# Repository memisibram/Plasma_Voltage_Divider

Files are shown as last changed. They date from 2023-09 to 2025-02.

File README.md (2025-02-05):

# Plasma_Voltage_Divider
Plasma Voltage Divider

### About the project
An electronic circuit for reading voltage from plasma machines.

Plasma machines output up to 200v. We need a voltage divider to read this voltage and use it in projects such as THC. This circuit gives output between 0 and 5v by dividing the voltage for use in controllers such as Atmega.

 - Video: [https://www.youtube.com/watch?v=IpVODe6NoKA](https://youtu.be/YBrCMQDwGMo)

### Drawing program
It was prepared using the Cross Platform and Open Source Electronics Design Automation Suite KiCad 6.0.

### Required components:
 - 2 x	5.1v - Zener Diode for D1,D2
 - 2 x	10µF/25V or 16v- Electrolytic Capacitor for C6,C7
 - 2 x	9x12 - 30mH Radial D9.5mm P5.00mm inductor for L1,L2
 - 4 x	1nF - Ceramic disc for C5,C2,C3,C4
 - 2 x	LM358 - op-amp for U1,U3
 - 1 x	100R - 1/4w or 1/2w for R5
 - 1 x	B1212S-1WR3 for BS1
 - 2 x	47k - 1/4w or 1/2w for R4,R6
 - 1 x	47nF 1KV  - High Voltage Ceramic Capacitor for C1
 - 1 x	HCNR200 - high-linearity analog optocoupler for U2
 - 1 x	3k9 - 5W - Power Resistor Ceramic Cement Resistor for R3
 - 2 x	100k - 5W - Power Resistor Ceramic Cement Resistor for R1,R2
 - 1 x	1x02_P5.00mm_Horizontal - Plasma Negative Electrode Terminal for J1
 - 1 x	1x02_P5.00mm_Horizontal - Plasma Positive Work Terminal for J3
 - 1 x	1x04_P5.00mm_Horizontal - Power / Output Terminal for J2

### Pictures

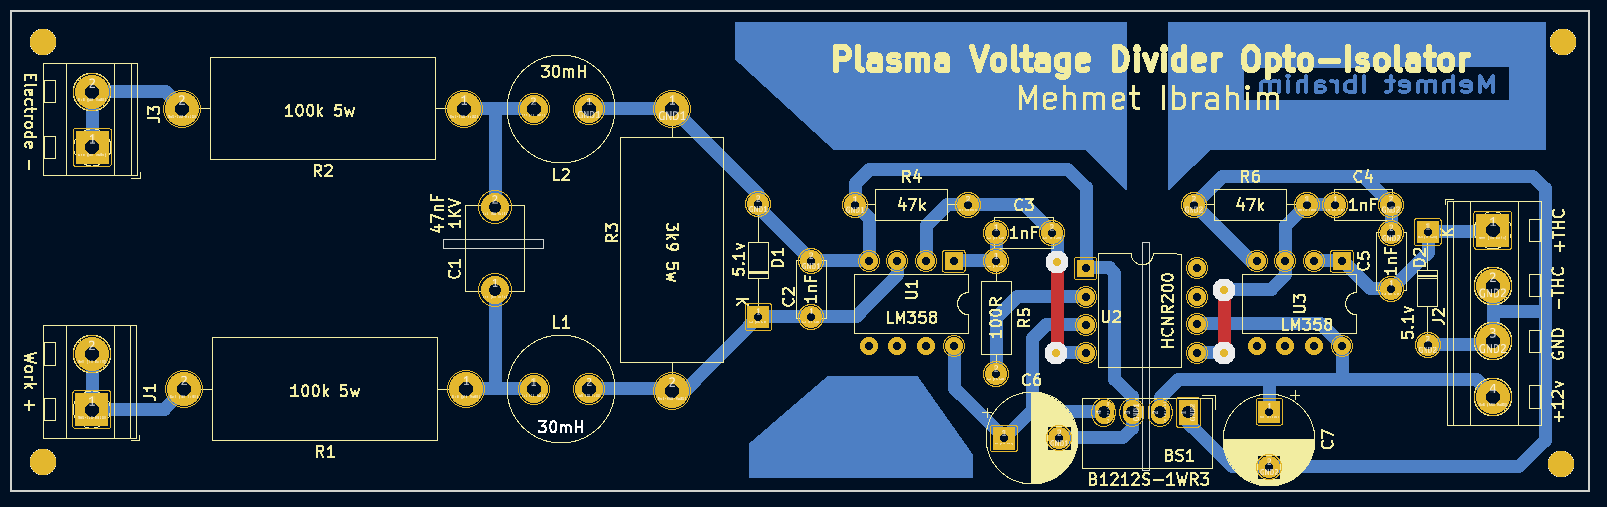
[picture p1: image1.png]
Plasma Voltage Divider Image1

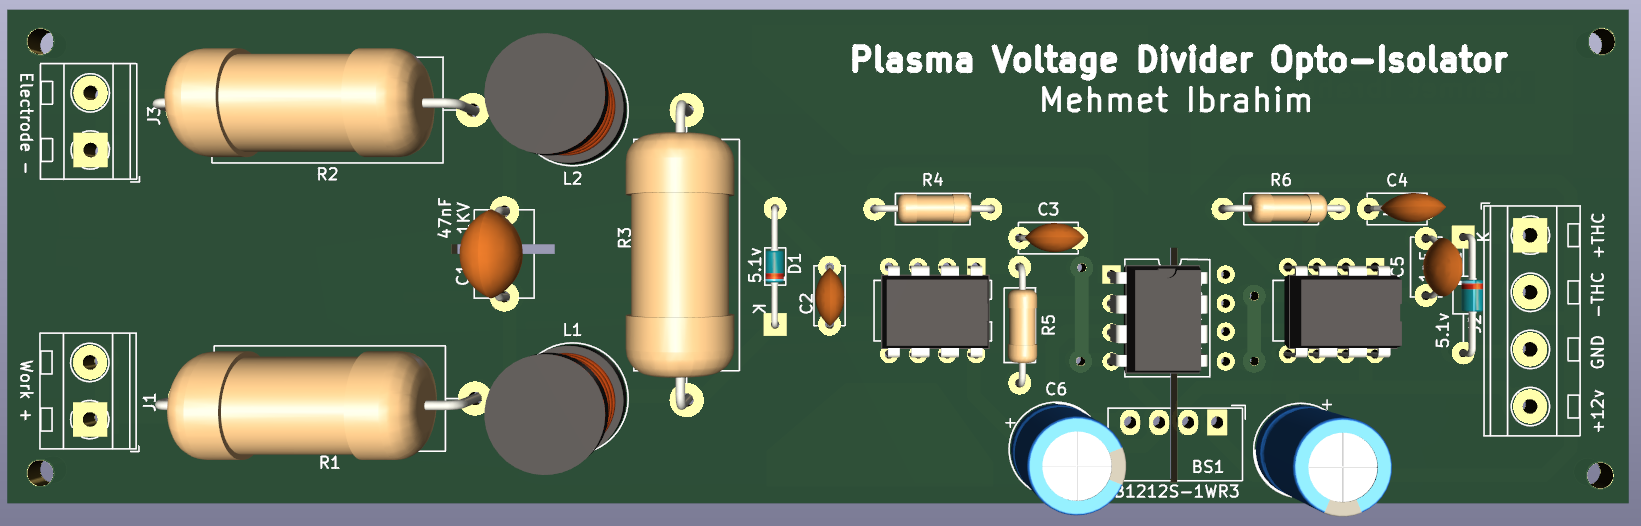
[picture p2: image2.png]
Plasma Voltage Divider Image2

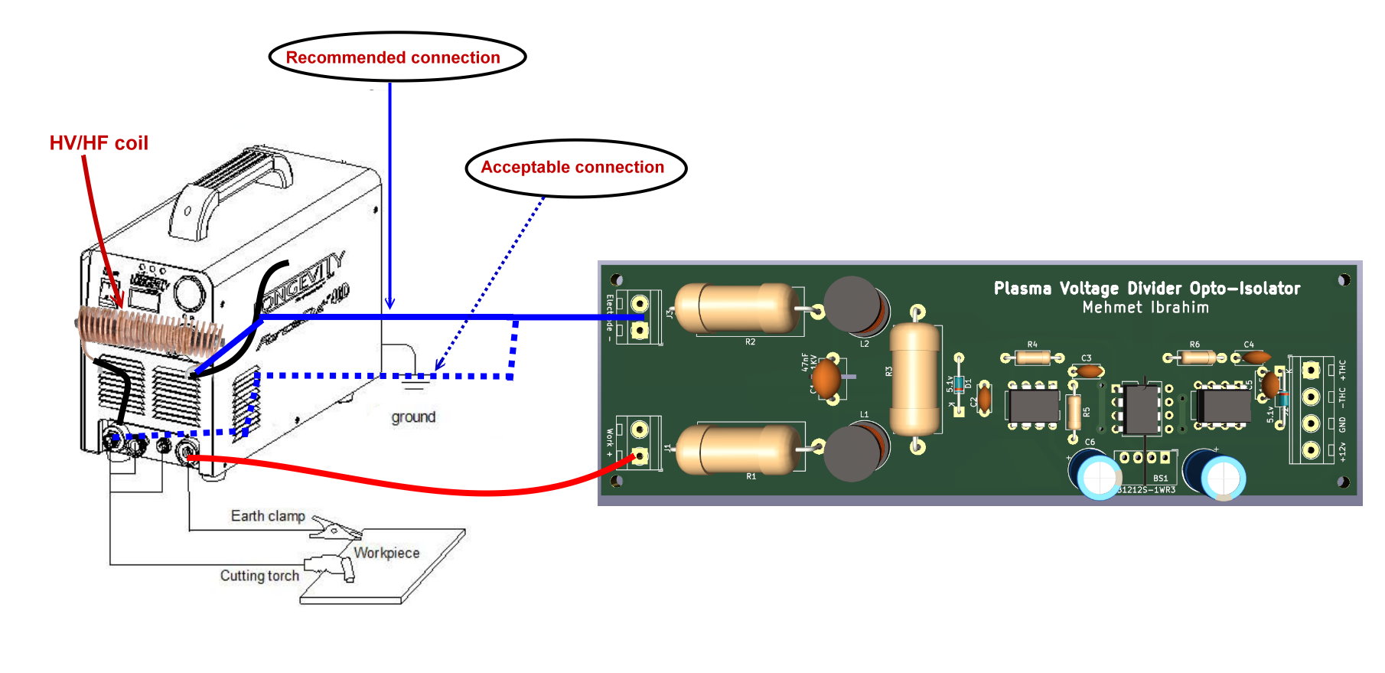
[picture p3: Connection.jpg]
Plasma Voltage Divider Image3


### License GNU GPL v3.0

### Donation

  -  Paypal: memisibram@gmail.com or https://www.paypal.me/memisibram

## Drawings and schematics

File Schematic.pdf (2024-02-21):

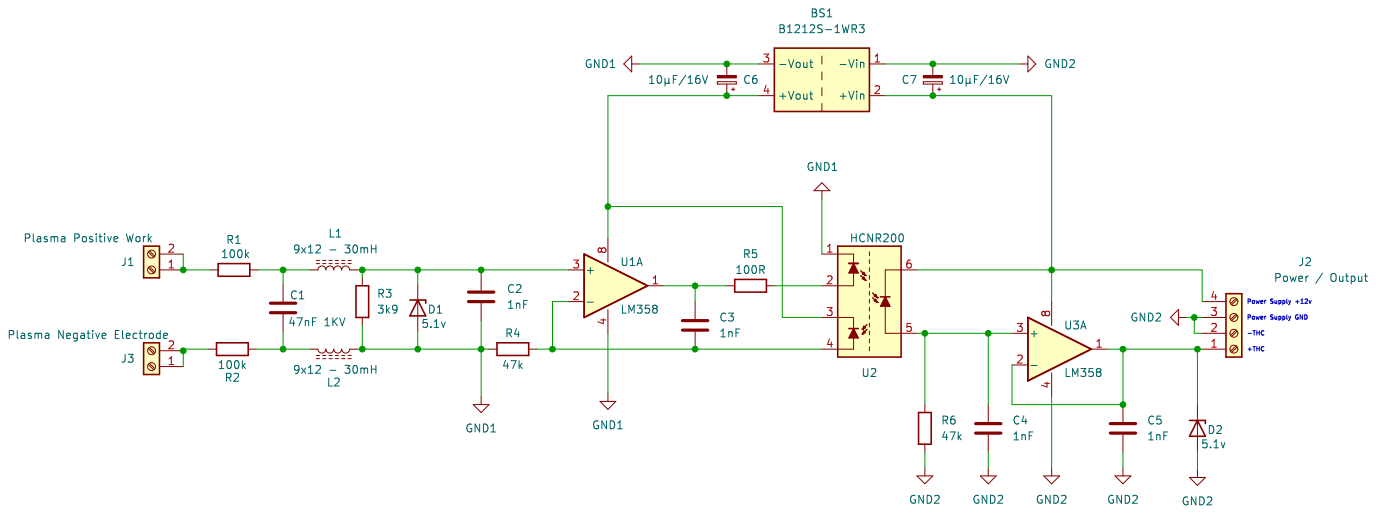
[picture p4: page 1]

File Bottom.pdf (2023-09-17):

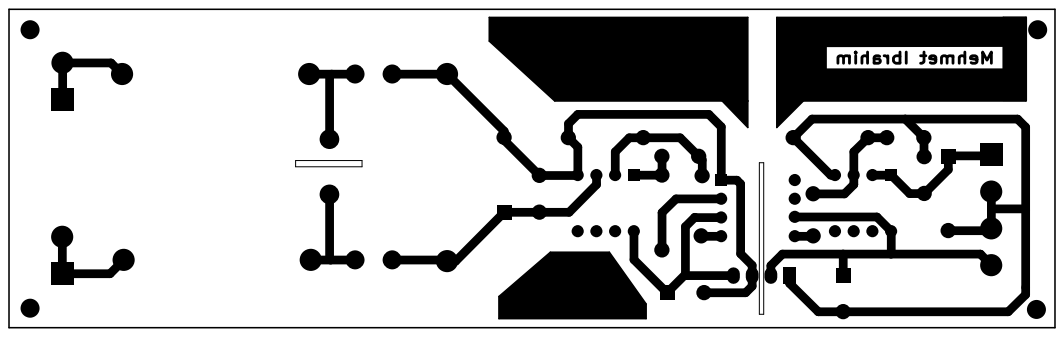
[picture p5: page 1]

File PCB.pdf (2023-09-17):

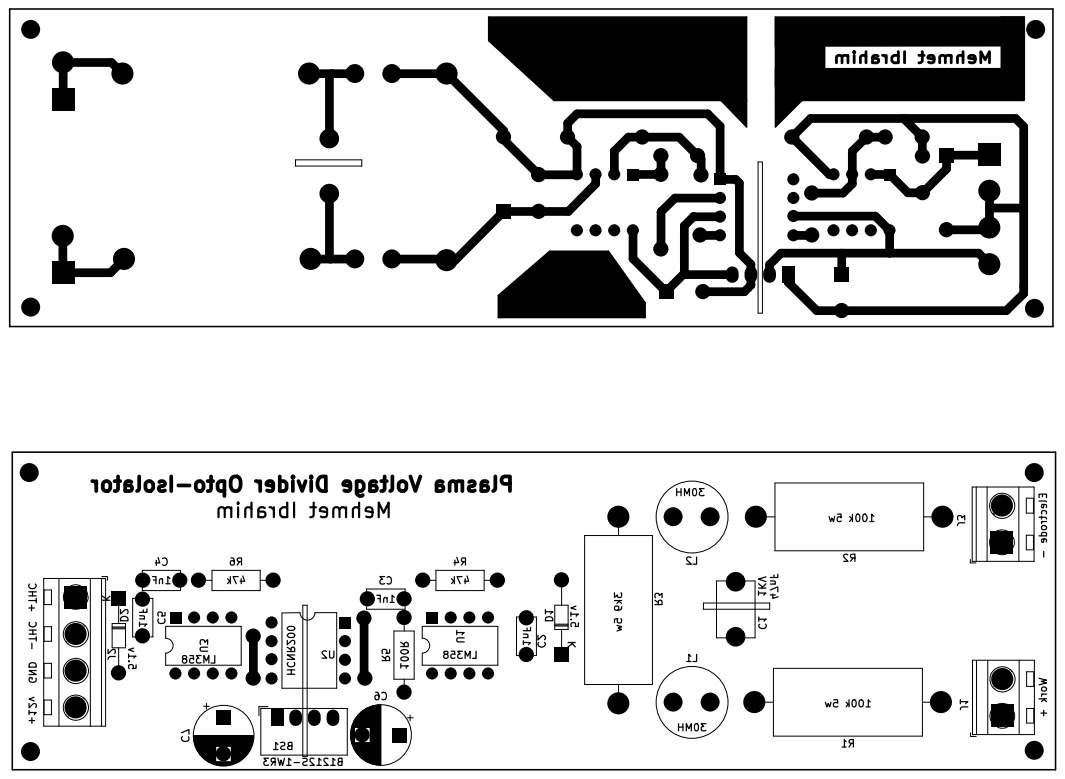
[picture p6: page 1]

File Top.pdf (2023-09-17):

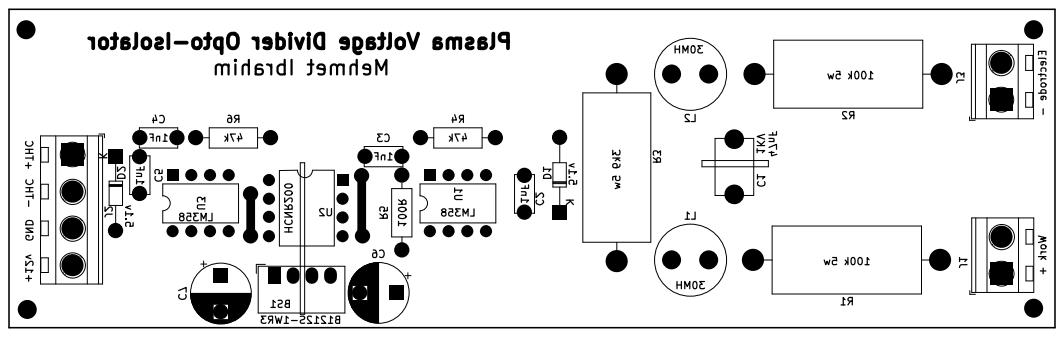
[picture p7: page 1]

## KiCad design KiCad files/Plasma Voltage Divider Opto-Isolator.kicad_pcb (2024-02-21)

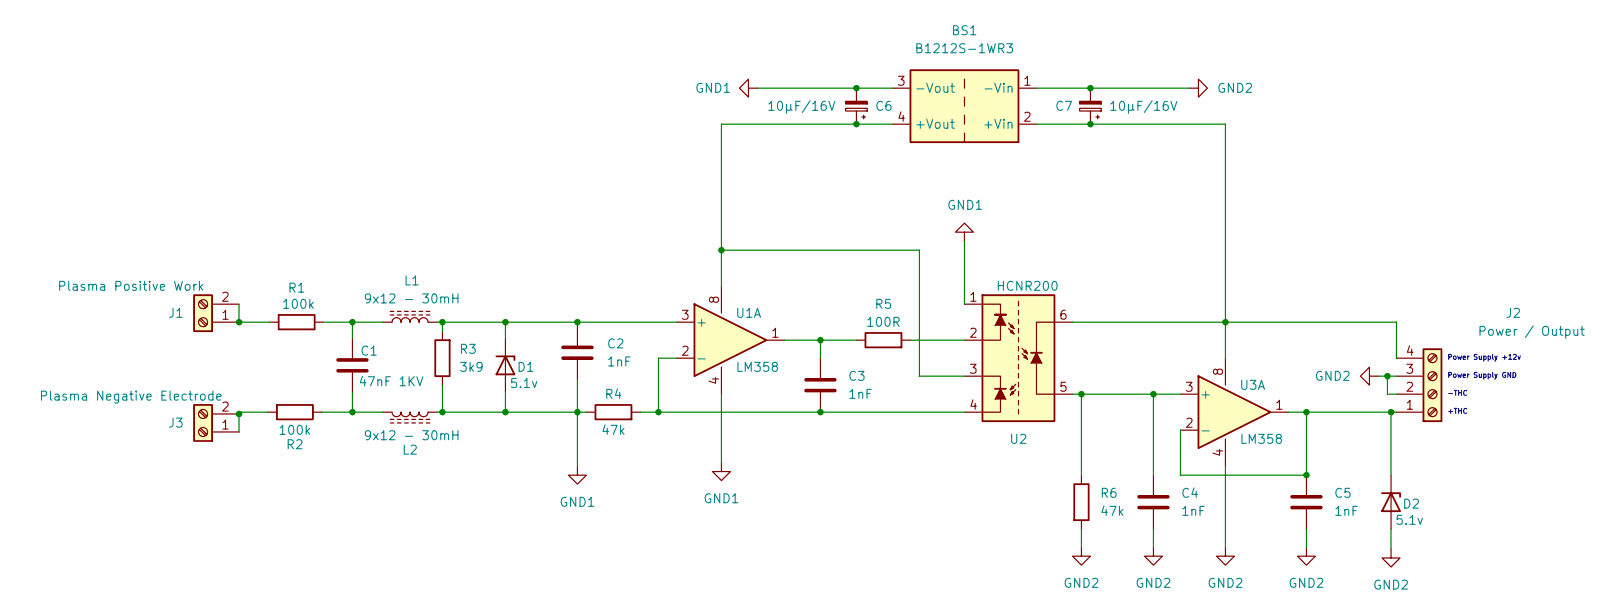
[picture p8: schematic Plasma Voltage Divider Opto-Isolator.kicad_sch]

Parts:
BS1: B1212S-1WR3; Converter_DCDC_Murata_MEE1SxxxxSC_THT
C1: 47nF 1KV; C_Disc_D7.5mm_W5.0mm_P7.50mm
C2, C3, C4, C5: 1nF; C_Disc_D5.0mm_W2.5mm_P5.00mm
C6, C7: 10µF/16V; CP_Radial_D8.0mm_P5.00mm
D1, D2: 5.1v; D_DO-34_SOD68_P10.16mm_Horizontal
J1: Plasma Positive Work; TerminalBlock_MetzConnect_Type094_RT03502HBLU_1x02_P5.00mm_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
J2: Power / Output; TerminalBlock_MetzConnect_Type094_RT03504HBLU_1x04_P5.00mm_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
J3: Plasma Negative Electrode; TerminalBlock_MetzConnect_Type094_RT03502HBLU_1x02_P5.00mm_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
L1, L2: 9x12 - 30mH; L_Radial_D9.5mm_P5.00mm_Fastron_07HVP
R1, R2: 100k; R_Axial_DIN0922_L20.0mm_D9.0mm_P25.40mm_Horizontal
R3: 3k9; R_Axial_DIN0922_L20.0mm_D9.0mm_P25.40mm_Horizontal
R4, R6: 47k; R_Axial_DIN0207_L6.3mm_D2.5mm_P10.16mm_Horizontal
R5: 100R; R_Axial_DIN0207_L6.3mm_D2.5mm_P10.16mm_Horizontal
U1, U3: LM358; DIP-8_W7.62mm
U2: HCNR200; DIP-8_W7.62mm

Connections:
GND1: BS1.3 (-Vout), C2.2, C6.2, D1.2 (A), L2.1, R3.1, R4.1, U1.4 (V-), U2.1
GND2: BS1.1 (-Vin), C4.2, C5.2, C7.2, D2.2 (A), J2.2, J2.3, R6.2, U3.4 (V-)
unnamed: BS1.2 (+Vin), C7.1, J2.4, U2.6, U3.8 (V+)
unnamed: BS1.4 (+Vout), C6.1, U1.8 (V+), U2.3
unnamed: C1.1, L1.1, R1.1
unnamed: C1.2, L2.2, R2.1
unnamed: C2.1, D1.1 (K), L1.2, R3.2, U1.3 (+)
unnamed: C3.1, R5.1, U1.1
unnamed: C3.2, R4.2, U1.2 (-), U2.4
unnamed: C4.1, R6.1, U2.5, U3.3 (+)
unnamed: C5.1, D2.1 (K), J2.1, U3.1, U3.2 (-)
unnamed: J1.1, J1.2, R1.2
unnamed: J3.1, J3.2, R2.2
unnamed: R5.2, U2.2

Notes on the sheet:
Power Supply GND
Power Supply +12v
-THC
+THC

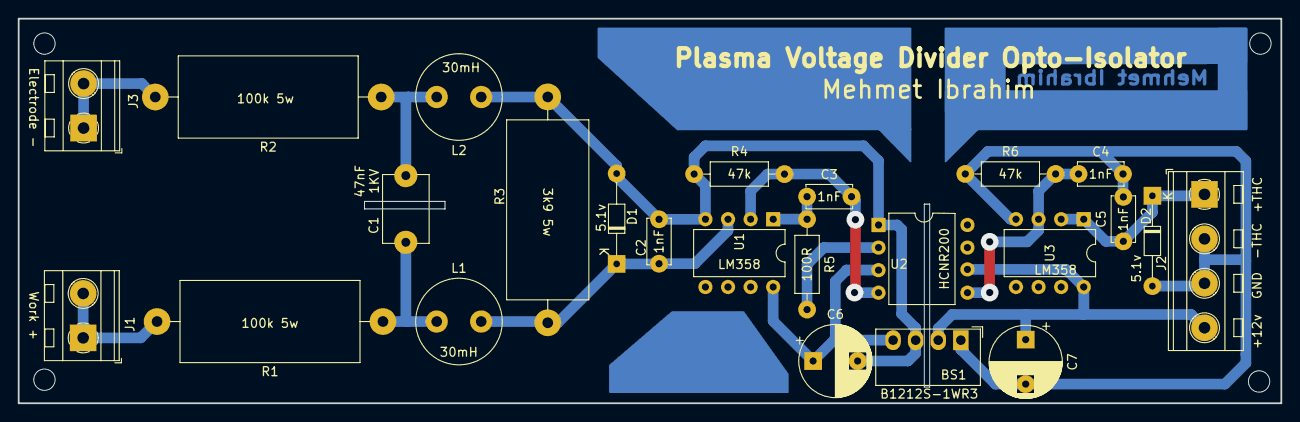
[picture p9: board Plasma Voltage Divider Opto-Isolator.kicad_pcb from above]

Board: 2 copper layers, 142.0 x 43.2 mm, 24 parts (0 on the bottom side), 14 nets.

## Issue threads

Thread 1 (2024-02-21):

inductors are noted as MEGA henries

VeryFastSnail, 2024-02-21:
in schematic and pcb design inductors are noted as Mega henries (MH) instead of mili henries (mH)

memisibram, 2024-02-21:
Yes that's right, you are a careful person, I will fix this.

Closed 2024-03-19.
